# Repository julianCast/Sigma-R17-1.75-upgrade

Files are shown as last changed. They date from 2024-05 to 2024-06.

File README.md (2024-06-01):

# Sigma-R17-1.75-upgrade

<p align="center">
  
</p>

Guia y recursos para convertir tu Sigma R16/R17 de 2.85 a 1.75 sin flasheo de firmware.

📖 Esta guia está basada en este proyecto https://www.printables.com/model/135803-bcn3d-sigma-upgrade-to-175mm, así que si te parece útil por favor déjales un comentario. Las piezas alojadas en la carpeta stl están sacadas de dicho proyecto.

## Materiales
Yo he optado por versiones de TriangleLab ya que son más económicos pero dejo enlaces para e3d también.
- 2x V6 metal only ([e3d](https://e3d-online.com/products/v6-hotend-metal-only), [trianglelab](https://es.aliexpress.com/item/32844028127.html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))
- 2x Fan Duct de E3D ([e3d](https://e3d-online.com/products/v6-fan-duct), incluido en V6 version trianglelab)
- 2x Extrusores Titan Extruder:
  - 1x estandar ([e3d](https://e3d-online.com/products/titan-extruder?variant=41261794033723), [trianglelab](https://es.aliexpress.com/item/1005003092239261.html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))
  - 1x mirrored ([e3d](https://e3d-online.com/products/titan-extruder?variant=31134336254011), [trianglelab](https://es.aliexpress.com/item/32993081695.html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))
- 2m Tubo Bowden Capricorn ([Amazon](https://www.amazon.es/dp/B089KMHC7S/ref=twister_B08PNM4J8T?_encoding=UTF8&psc=1))

## Piezas impresión
Imprimir todo lo que esta en carpeta ´stl´, en filamento PETG, con 60% infill, y 4 walls.

## Pasos de montaje
### 1. Extrusor
Comienza con el extrusor izquierdo (principal). Reemplaza el extrusor actual por el nuevo, conservamos el motor de Sigma. La muela de extrusión puede que este atascada, posiblemente tengas que taladrar el tornillo de paso.

⚠️ Dado que los nuevos extrusores sobresalen algo más que anteriores, tenemos que corregir el y-endstop para evitar choque. Para ello buscamos donde está la superficie que activa dicho endstop y le pegamos la pieza `y-endstop-extension.stl`, eso activará el endstop 4cm antes.

### 2. Hotend
No se reemplaza ni thermistor ni cable calentador. Una vez todo colocado deberia quedar casi igual de altura que el anterior (respecto distancia boquilla - endstop).

### 3. Tubo Capricornio
Reemplazar actual tubo 2.85 con 1.75, a excepción del tubo usado bajo filamento para guiarlo, ahi cortamos y metemos el 1.75 dentro del existente, así mantenemos el sistema actual.

## Ajustes de G-Code

### Diámetro Filamento
Seteamos a nivel configuracion de impresora el nuevo diámetro del filamento 1.75.
```gcode
M200 D1.75
```

### E-steps
Este motor tiene un ratio diferente al anterior asi que debemos re ajustar los pasos, sigue cualquier [tutorial](https://all3dp.com/2/extruder-calibration-calibrate-e-steps/) para ello. Como ejemplo, a mi me dio 422:
```gcode
M92 E422  ; Numero de pasos para el nuevo extrusor.
M500      ; Graba la configuración en la impresora.
```
### Y-axis home offset
Ya que hemos cambiado anteriormente el y-endstop, ahora debemos cambiar los settings de home de la maquina para que no se choque con el frame frontal.
```gcode
M206 Y-40 ; Y-axis home offset a -40 mm.
M500      ; Graba la configuración en la impresora.
```

## Ajustes Cura Slicer

### Impresora
Añadimos nueva custom FFF printer con los siguientes parámetros, recuerda en la pestaña de Extruders cambiar a 1.75:



### Profile
Ahora toca añadir [el perfil de calidad](https://github.com/julianCast/Sigma-R17-1.75-upgrade/blob/main/Sigma_175_fine.curaprofile) que he montado para este mod,  luego en Cura lo importamos:



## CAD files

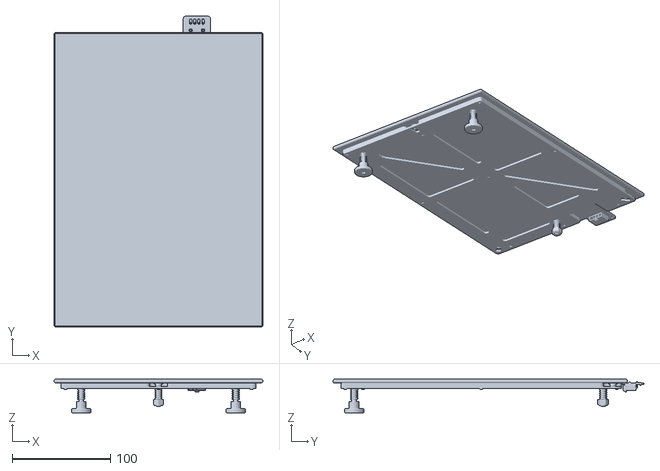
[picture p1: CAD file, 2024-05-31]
cura/resources/meshes/bcn3dsigma_bed.stl
212.0 x 316.0 x 34.1

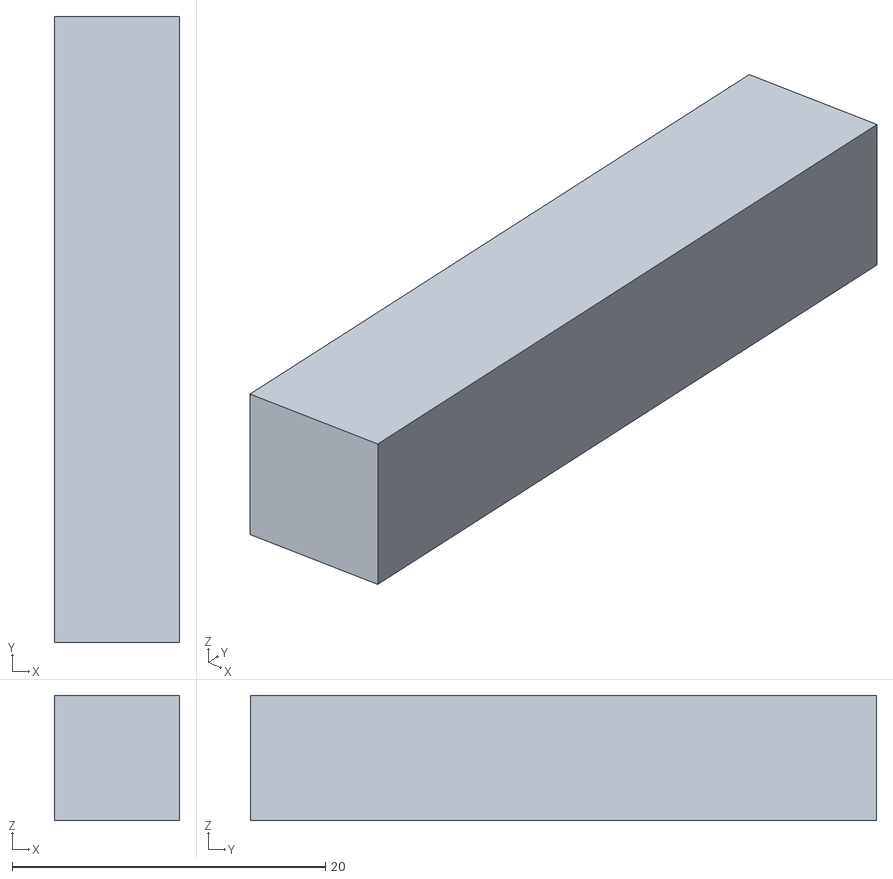
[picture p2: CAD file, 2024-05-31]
stl/y-endstop-extension.stl
8.00 x 40.0 x 8.00

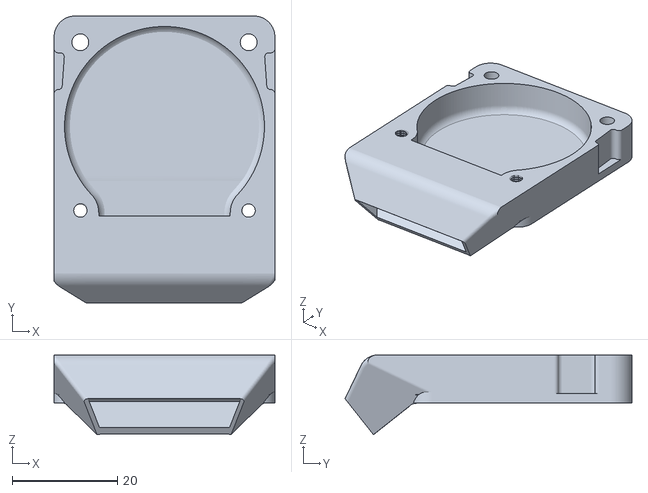
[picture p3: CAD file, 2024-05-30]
stl/Soporte_ventilador.stl
42.0 x 54.6 x 15.1

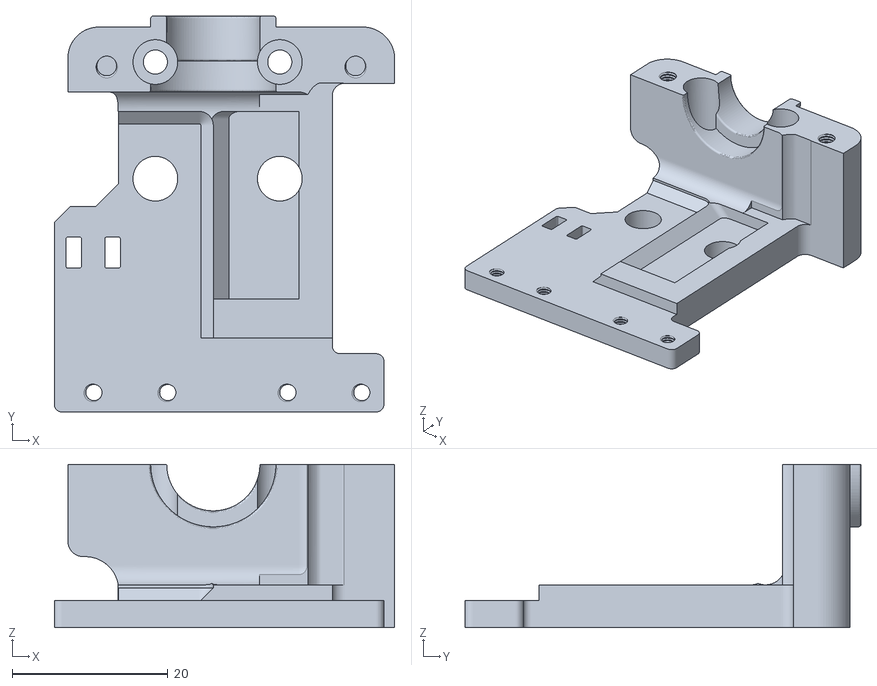
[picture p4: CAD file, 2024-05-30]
stl/Soporte_V6A.stl
43.8 x 50.9 x 21.0

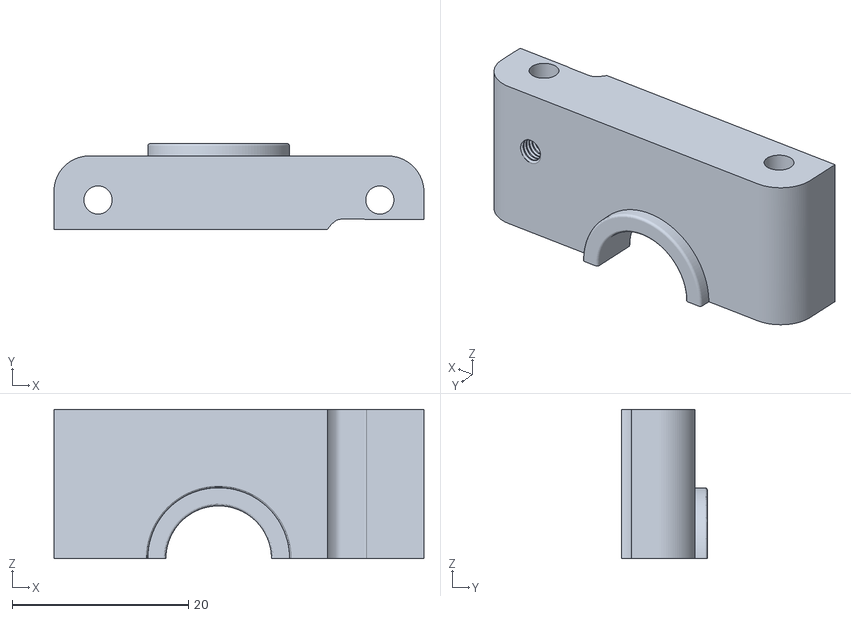
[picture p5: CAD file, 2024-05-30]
stl/Soporte_V6B.stl
42.0 x 9.77 x 17.0
